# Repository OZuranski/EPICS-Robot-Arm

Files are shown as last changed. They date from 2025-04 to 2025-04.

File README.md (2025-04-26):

# Project Manus
 
Project Manus is a student lead team part of Purdue University's EPICS ECE Outreach program. Our main goal with Project Manus is to showcase engineering design principles to prospective students through an interactive, easy to build robotic arm. The arm was modeled in Fusion 360 with mostly 3D printed parts and common electronics to remain accessible for schools and hobbyists. It features 5 degrees of freedom, RC controls, and Nema 17 stepper motors, all controled by an Arduino for expandibility. The endeffector can be replaced with various attatchments such as a claw or a pen. [Demo](https://drive.google.com/file/d/1h7FeMoHUVKW86da__4PCTzvnMPEXpfWK/view?usp=sharing)

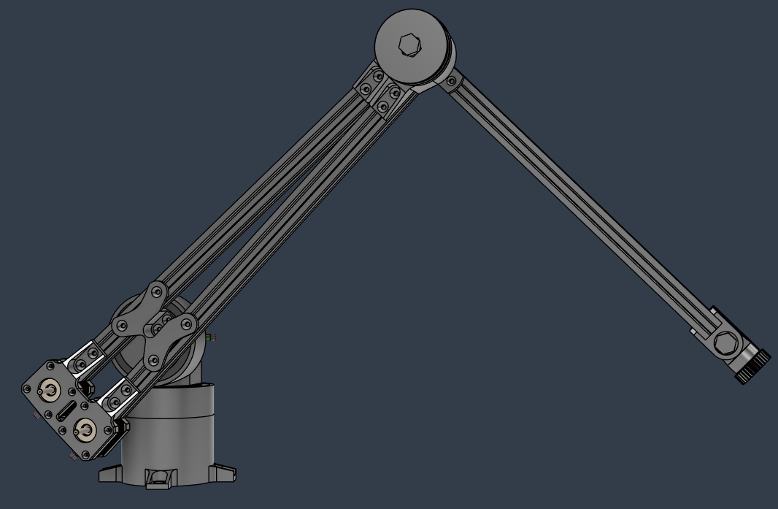
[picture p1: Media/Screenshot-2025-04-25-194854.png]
CAD

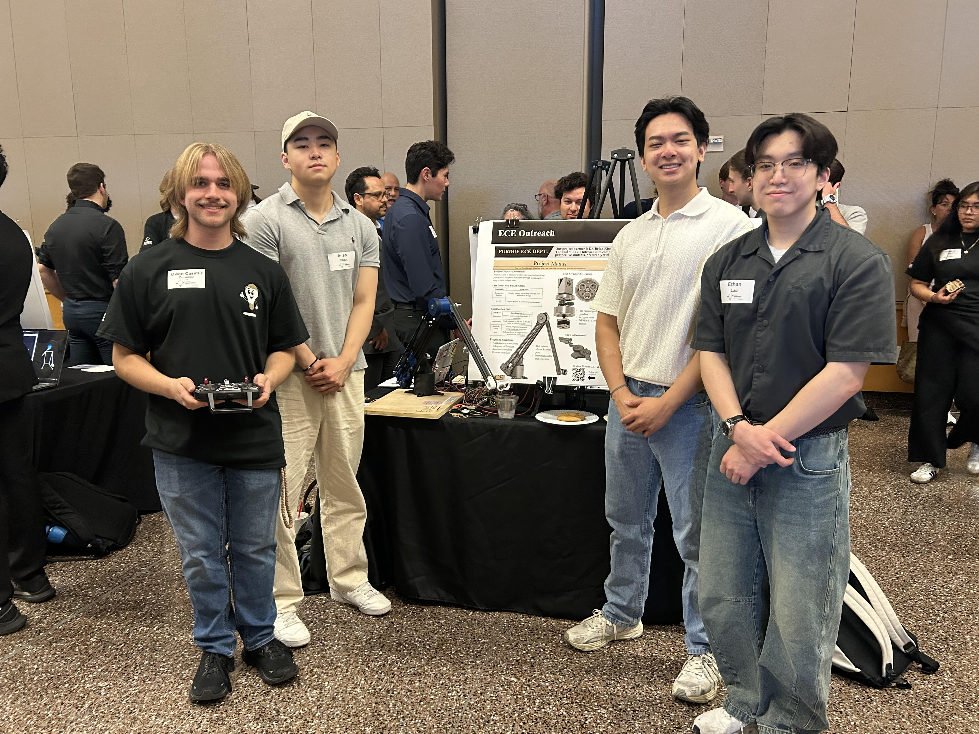
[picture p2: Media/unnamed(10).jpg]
Showcase

Poster
# Issues

1. Many components such as the bearings rely on a tight interference fit with 3D printed plastic. This method makes assembly relatively simple, however it makes disassembly almost impossible without cracking the plastic. If the parts are printed in PLA, the fit can slowly  loosen over time due to PLA's fluid properties under pressure, leading to excessive play in the arm. We suggest modifying the model to include screw sections between press fit components and other parts to make disassembly easier, and to print all parts in PETG.
2. The gear ratio of the base, shoulder, and elbow joint is not high enough for the weight of the arm. It is currently at 6:1, but we suggest modifying the gears within the planetary gearboxes and the pulleys to be at least 24:1. Geared Nema 17 or larger motors can be used, but this will require a major redesign of the arm which will be more costly.
3. Unfortunately due to time constraints within our semester, we were unable to fully implement the wrist joint, hand joint, and a functional end effector in our prototype. We suggest finding or desining a simple claw mechanism that uses light servo motors to minimize weight at the end of the arm.

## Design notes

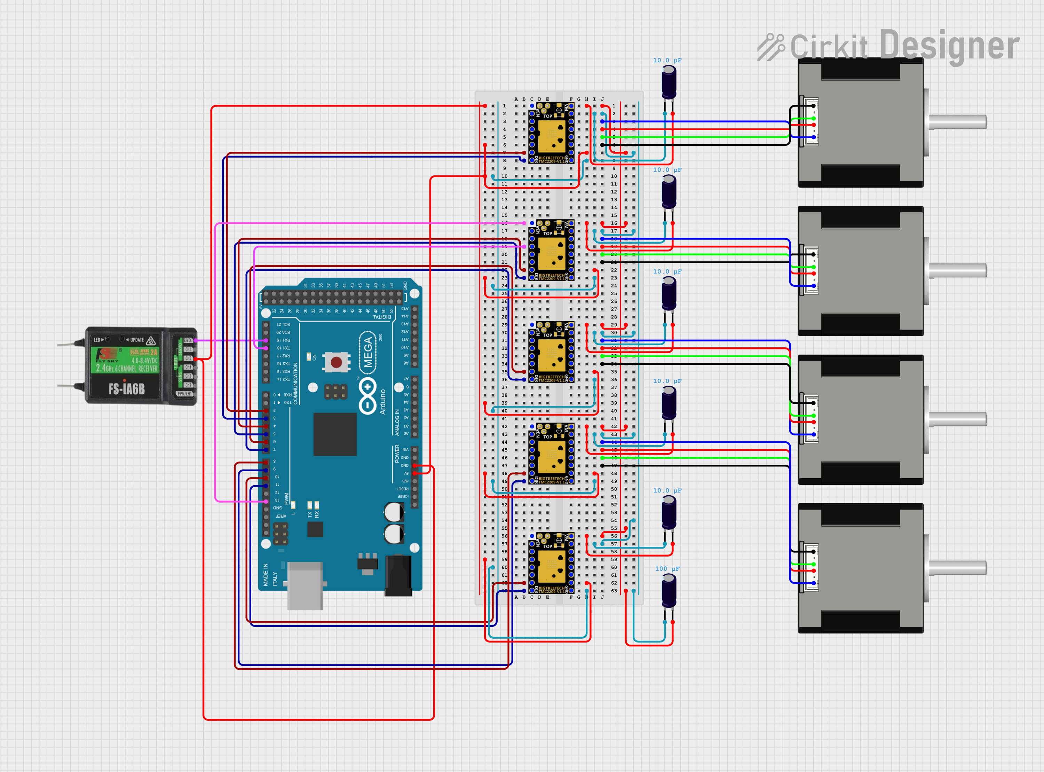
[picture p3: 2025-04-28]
Media/circuit_image.png

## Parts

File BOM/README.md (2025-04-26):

# Bill of Materials
 
The estimated build cost for the project is roughly $300. We reccomend printing all parts in PETG filament with standard settings. Please note that every 3D printer prints with a different tolerance. You will likely have to adjust dimesions within CAD to get proper interference fits, which this design relies on. A total of 6 planet gears and 2 sun gears are required.

1x $9.99 - GT2 Timing Belt  https://a.co/d/6Wf6PmA 

1x $7.69 - M10 Bolt https://a.co/d/aXNfsUf 

1x $5.99 - M10 Jam Nut https://a.co/d/iorE0f6 

1x $13.49 - 10x20 bearing https://a.co/d/e00AVKj 

1x $7.99 - 16t GT2 Pulley https://a.co/d/gQsRvjb 

1x $8.99 - 30x47 bearing https://a.co/d/8ohwXap 

1x $42.99 - Set of 5 Nema 17 motors https://a.co/d/6YtVc1i 

1x $13.79 - 60x78 bearings https://a.co/d/6YtVc1i 

1x $19.98 - Nema 11 motor https://a.co/d/0j2qDxP 

1x 20.99 Arduino MEGA 2650 https://a.co/d/017Ihgk 

1x $50.69 Wireless Controller https://a.co/d/4oq5mv8 

1x $19.98 set of 5 motor drivers https://a.co/d/9IKwbep 

1x $14.99 Machine screw set  https://a.co/d/8UwfHxt 

1x $18.59 2020 Aluminum extrusion  https://a.co/d/4guqIsl 

1x $5.99 M4 T nuts  https://a.co/d/hmVDdFK 

1x $4.99 M4 x 35mm screws https://a.co/d/f0rgOdL 

1x $4.99 m2.5 x 8mm screws https://a.co/d/42wxDNc

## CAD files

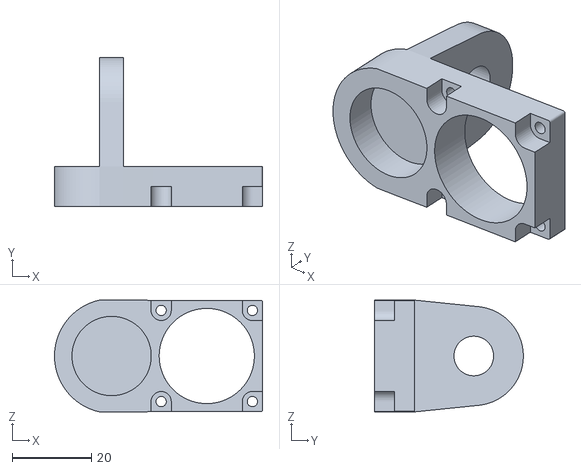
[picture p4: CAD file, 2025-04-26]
BOM/Printed Parts/Hand bracket.stl
52.5 x 37.5 x 28.2

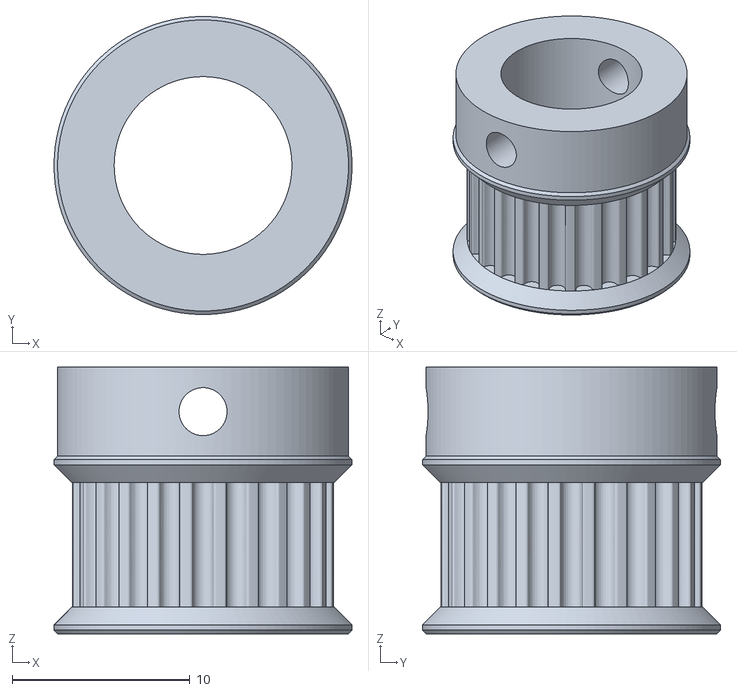
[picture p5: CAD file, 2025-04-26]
BOM/Printed Parts/Wrist Pulley 24t.stl
16.8 x 16.8 x 15.0

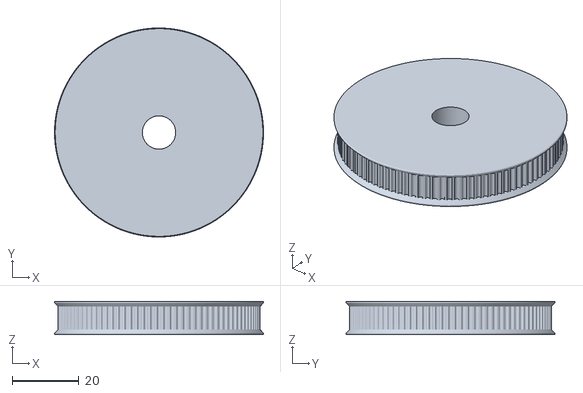
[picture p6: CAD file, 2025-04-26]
BOM/Printed Parts/Wrist Pulley 96t.stl
62.6 x 62.6 x 10.0

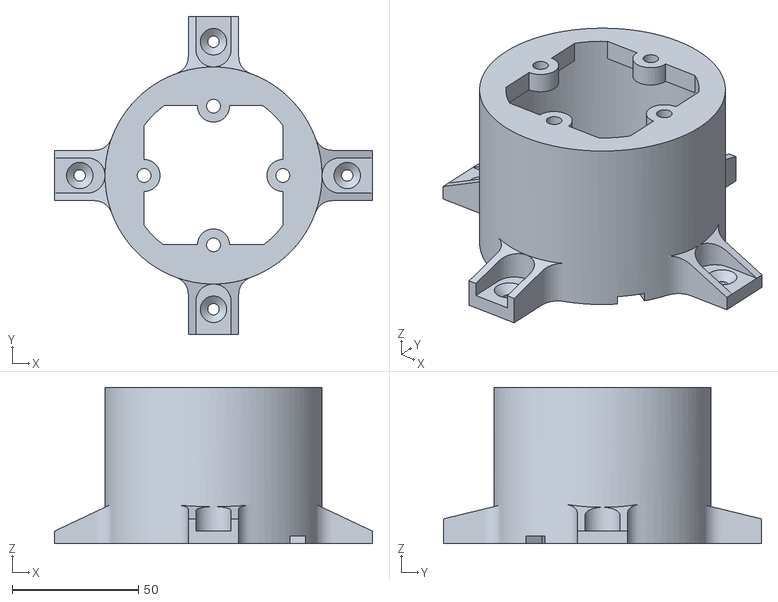
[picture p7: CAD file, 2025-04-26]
BOM/Printed Parts/Base Mount.stl
126.0 x 126.0 x 62.0

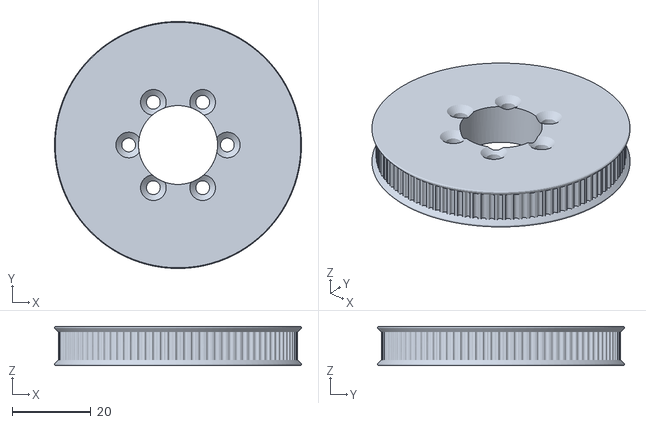
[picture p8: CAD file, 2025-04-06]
BOM/Printed Parts/Forearm Pulley 96t.stl
62.6 x 62.6 x 10.0

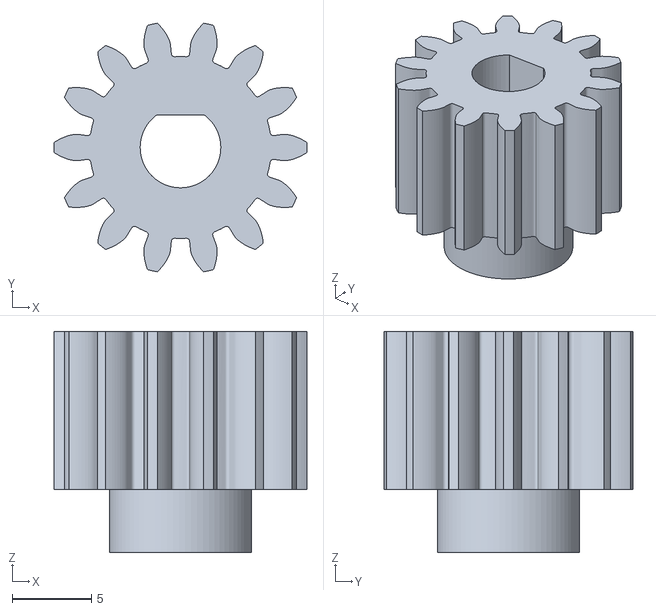
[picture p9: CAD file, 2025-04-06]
BOM/Printed Parts/Sun gear.stl
16.0 x 15.7 x 14.0

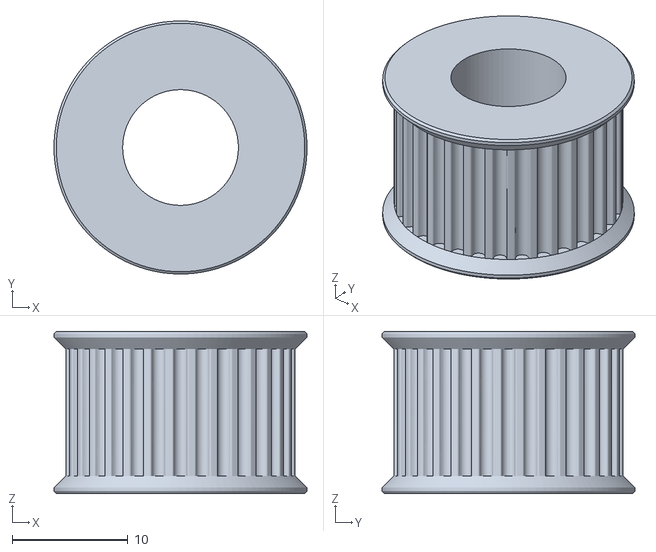
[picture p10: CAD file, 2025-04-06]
BOM/Printed Parts/Wrist Pulley 32t.stl
21.9 x 21.9 x 14.0

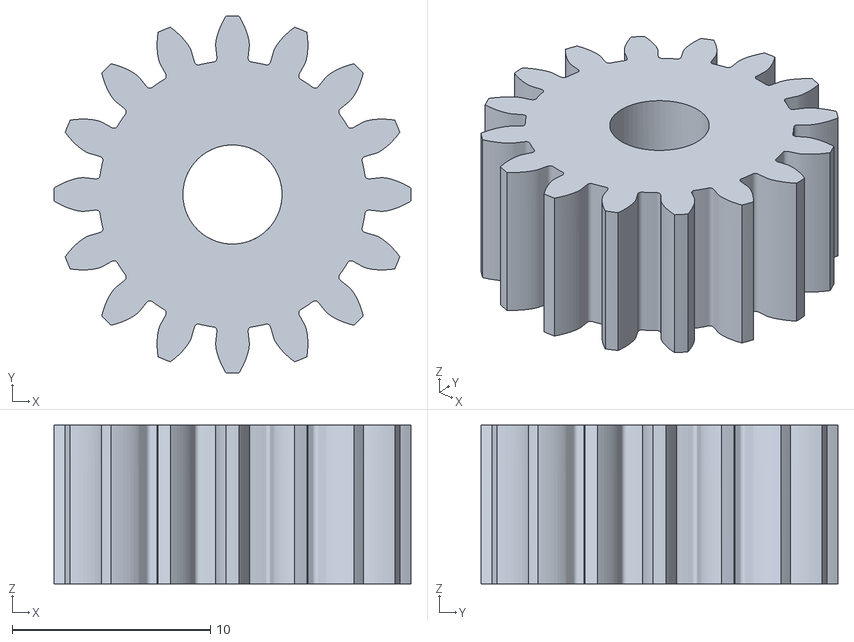
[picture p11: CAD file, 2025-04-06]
BOM/Printed Parts/Hand Gear 16t.stl
18.0 x 18.0 x 8.00

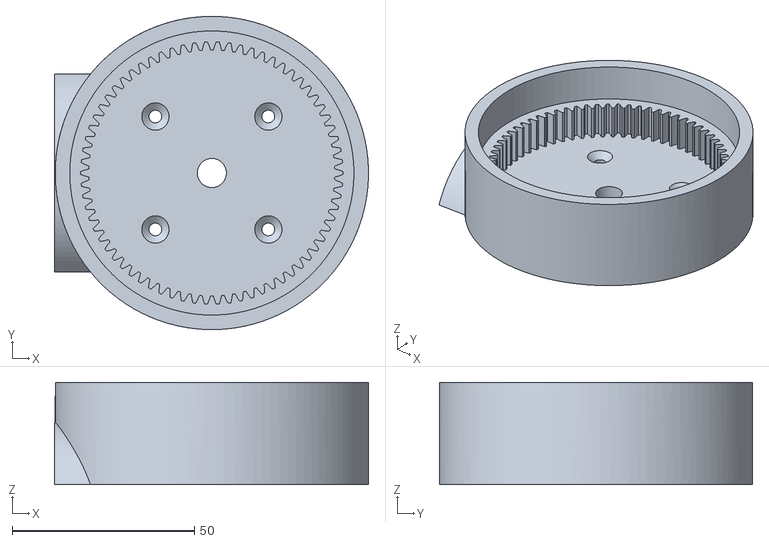
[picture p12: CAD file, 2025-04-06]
BOM/Printed Parts/Ring Gear Shoulder.stl
86.2 x 86.0 x 28.0

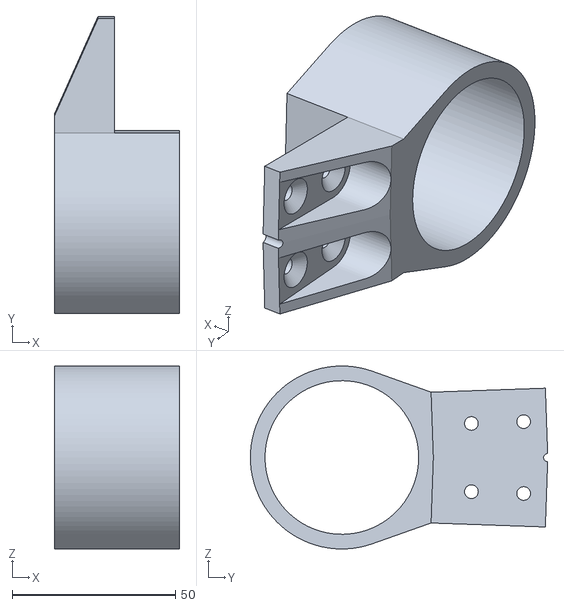
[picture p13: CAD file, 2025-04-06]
BOM/Printed Parts/Elbow Housing.stl
38.4 x 91.0 x 56.0

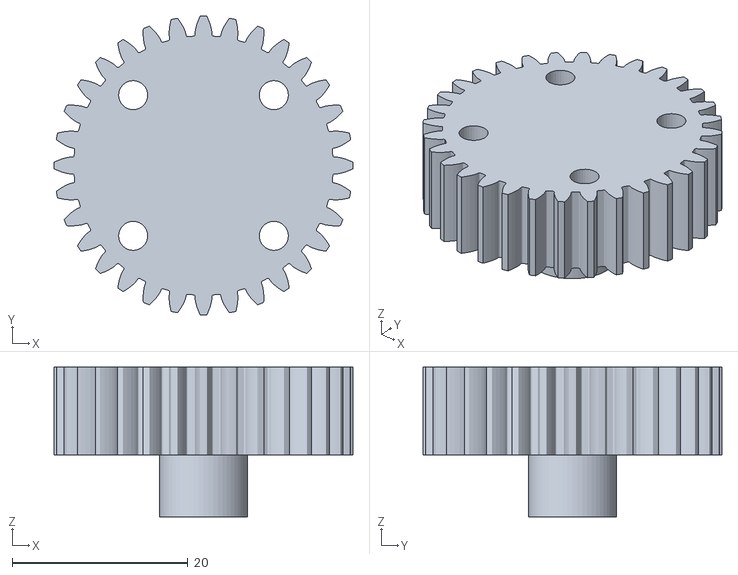
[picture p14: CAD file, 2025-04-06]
BOM/Printed Parts/Hand Gear 32t.stl
34.0 x 34.0 x 17.0

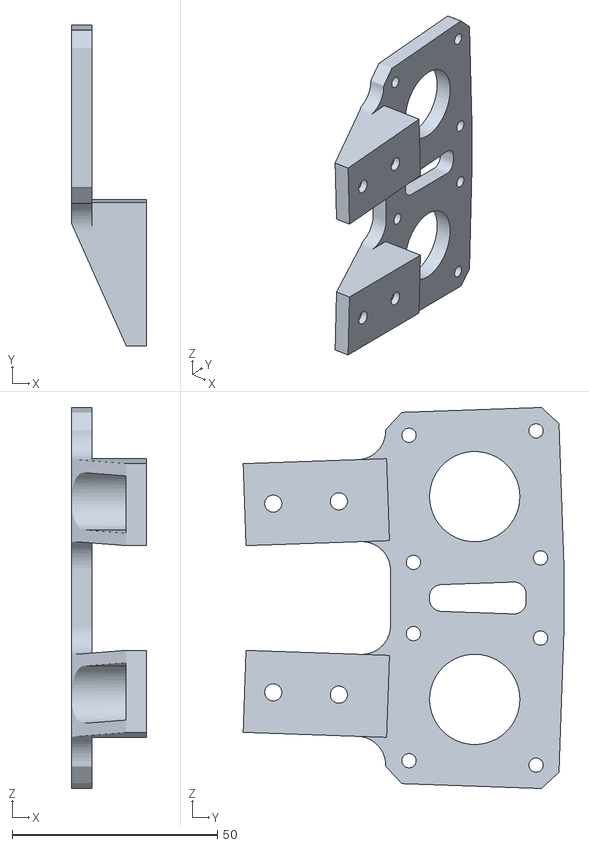
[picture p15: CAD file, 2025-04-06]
BOM/Printed Parts/Dual Motor Mount.stl
18.4 x 78.2 x 92.9

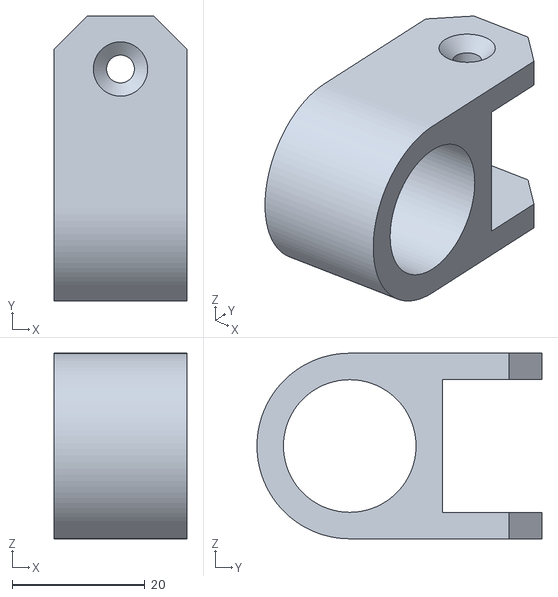
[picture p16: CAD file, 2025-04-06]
BOM/Printed Parts/Wrist Housing.stl
20.0 x 43.0 x 28.0

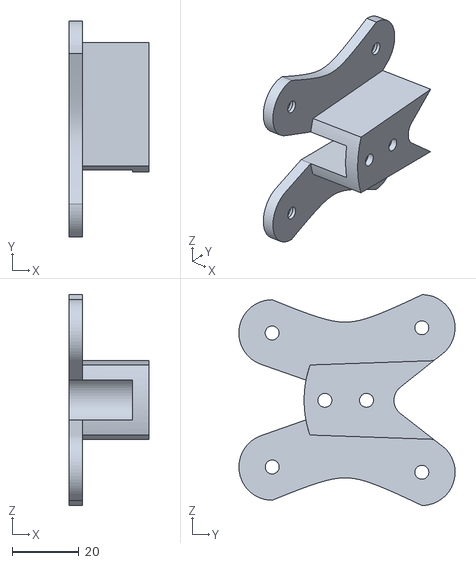
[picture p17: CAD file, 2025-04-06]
BOM/Printed Parts/Shoulder Bracket.stl
24.0 x 65.0 x 63.4

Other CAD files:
BOM/Printed Parts/Base Cage.stl
BOM/Printed Parts/Ring Gear Base.stl
BOM/Printed Parts/Forearm Attatchment.stl
BOM/Printed Parts/Shoulder Cage.stl
BOM/Printed Parts/Planet gear 28t.stl
BOM/Printed Parts/Shoulder Motor Bracket.stl
CAD/Manus Claw v1.f3d

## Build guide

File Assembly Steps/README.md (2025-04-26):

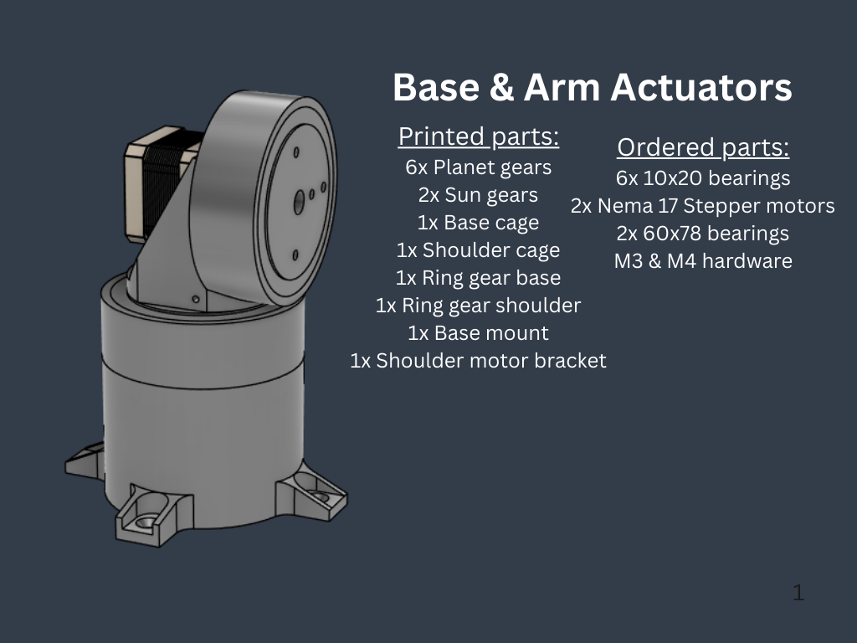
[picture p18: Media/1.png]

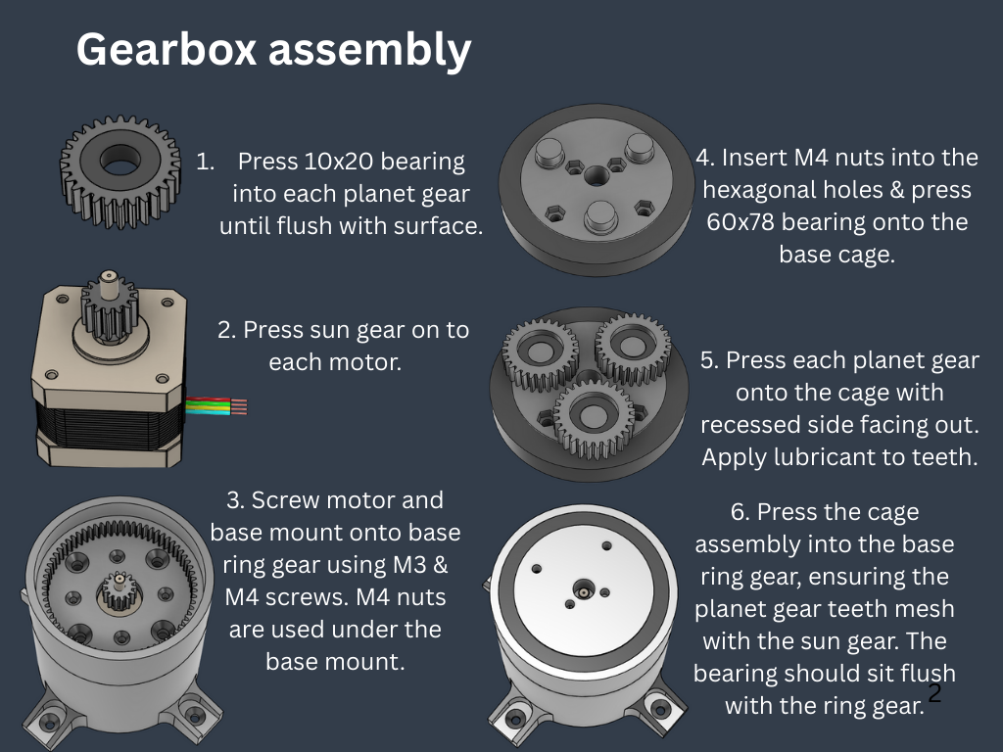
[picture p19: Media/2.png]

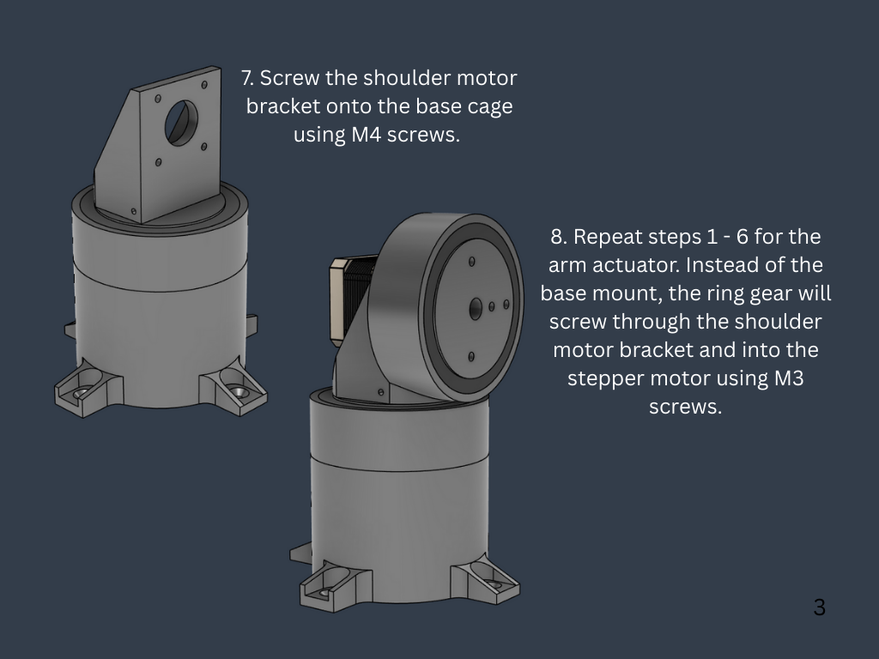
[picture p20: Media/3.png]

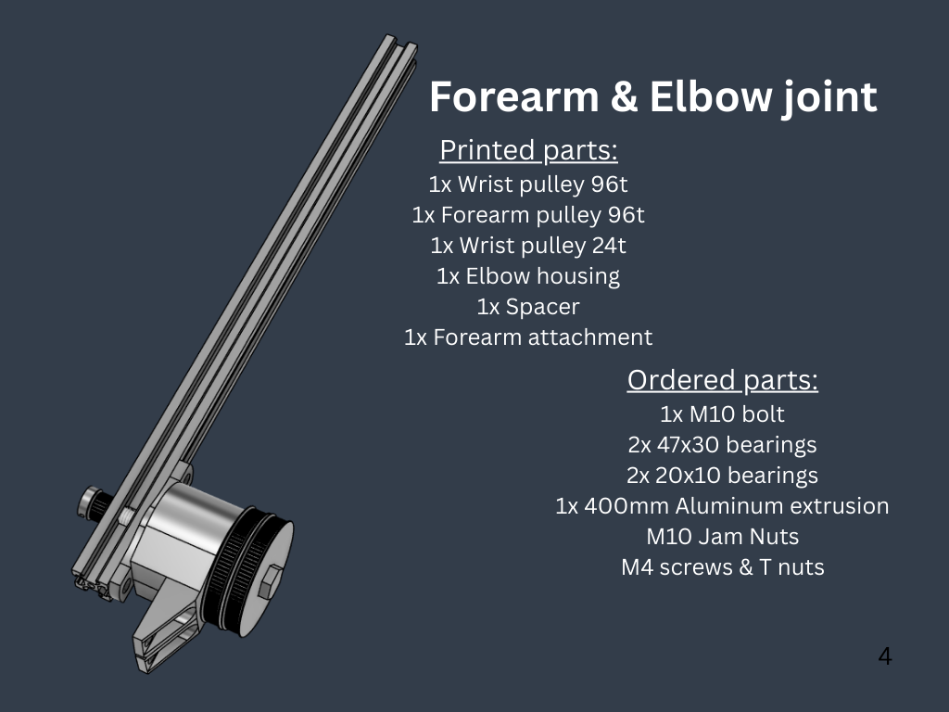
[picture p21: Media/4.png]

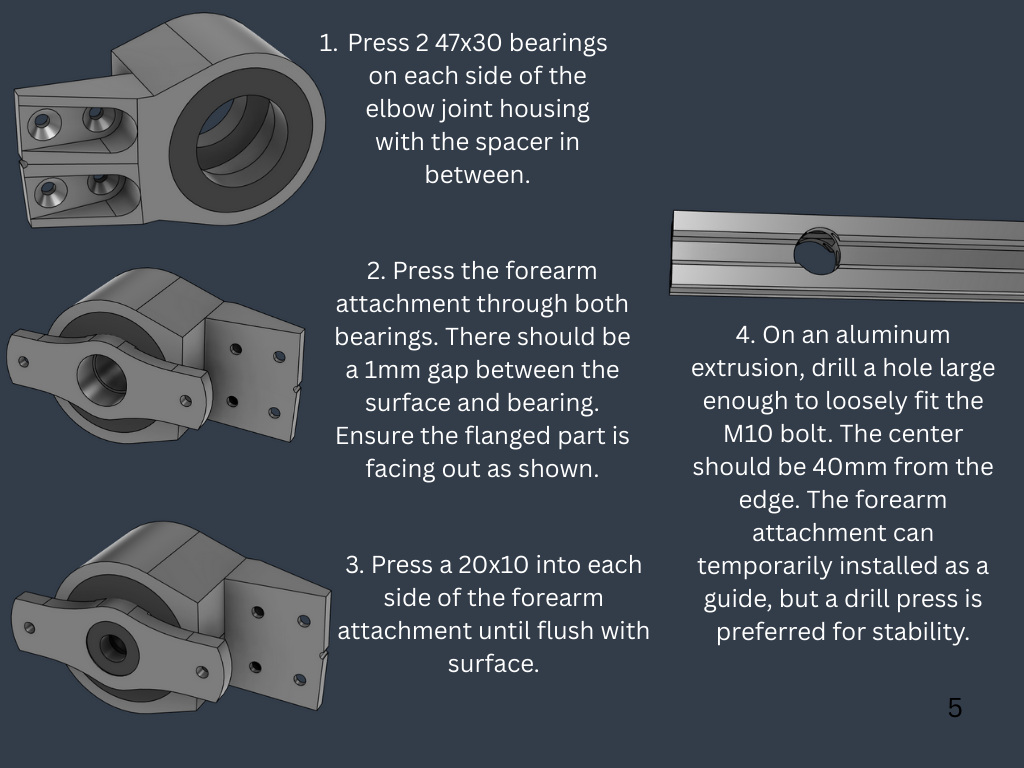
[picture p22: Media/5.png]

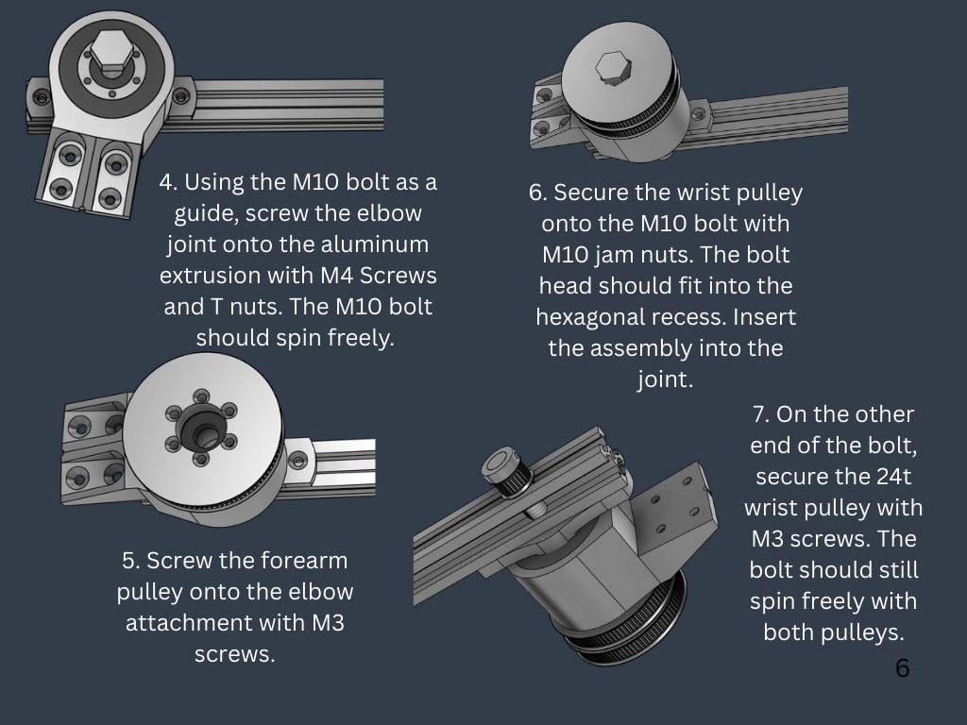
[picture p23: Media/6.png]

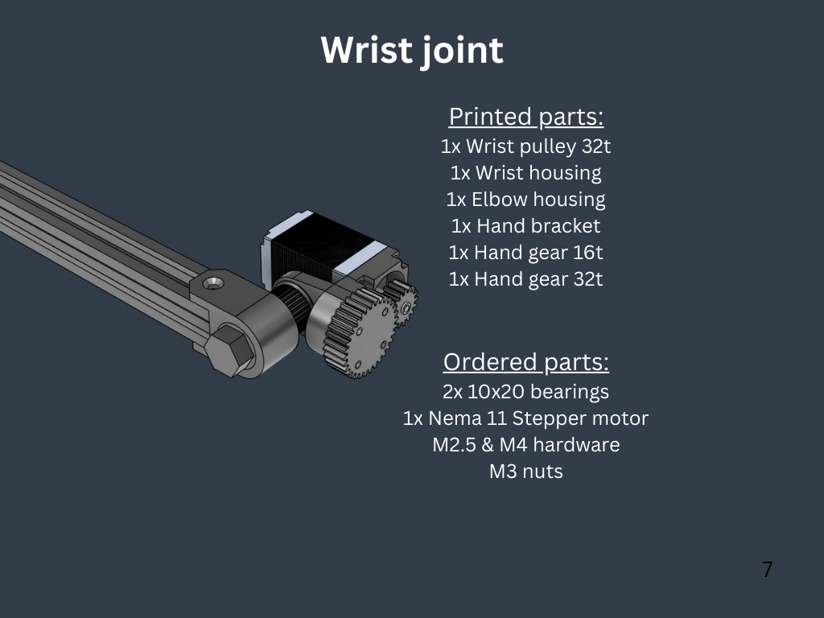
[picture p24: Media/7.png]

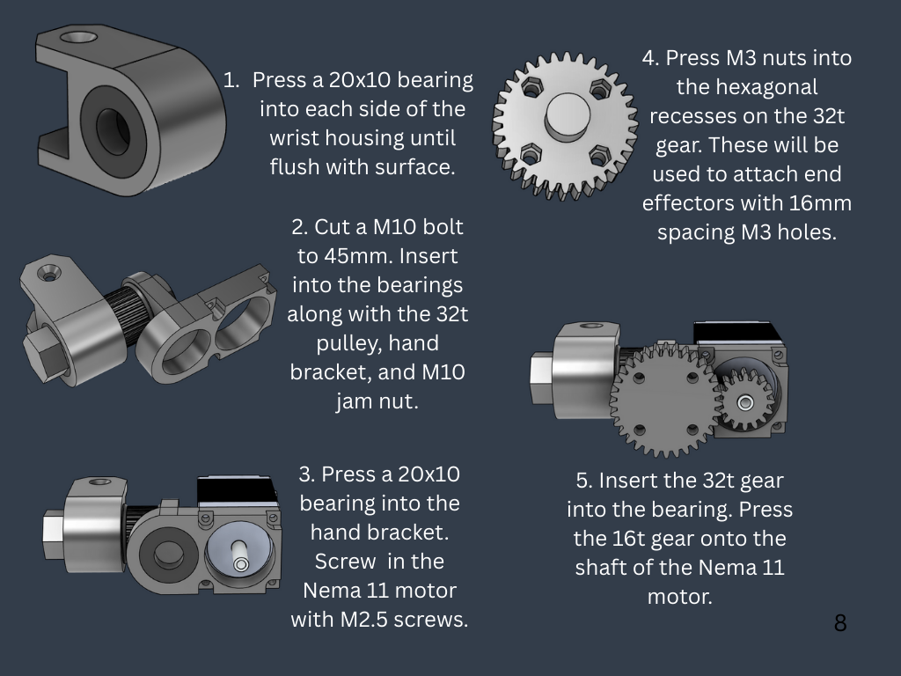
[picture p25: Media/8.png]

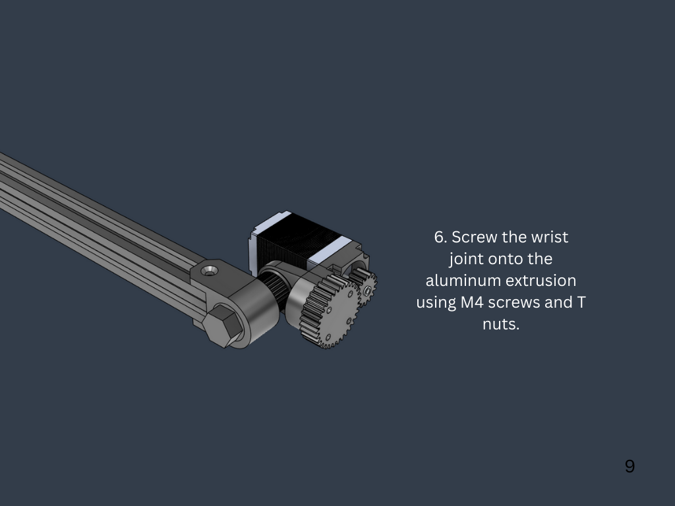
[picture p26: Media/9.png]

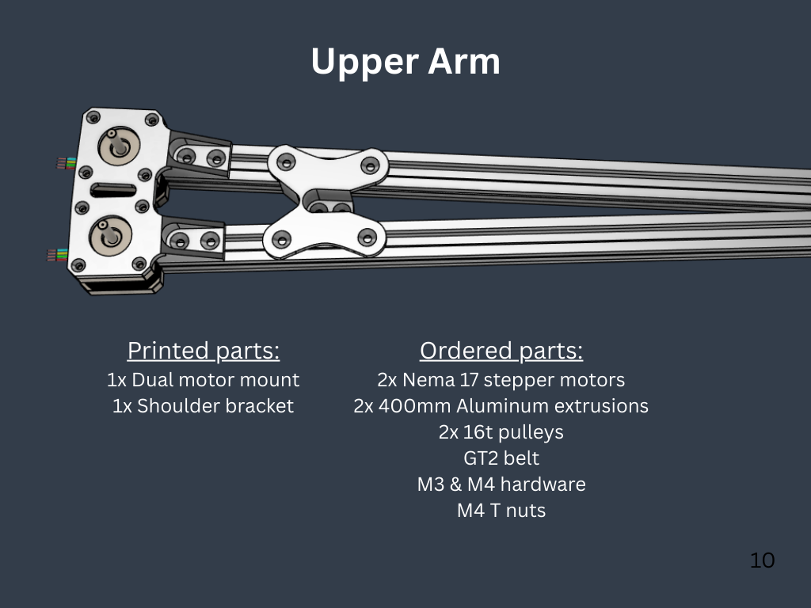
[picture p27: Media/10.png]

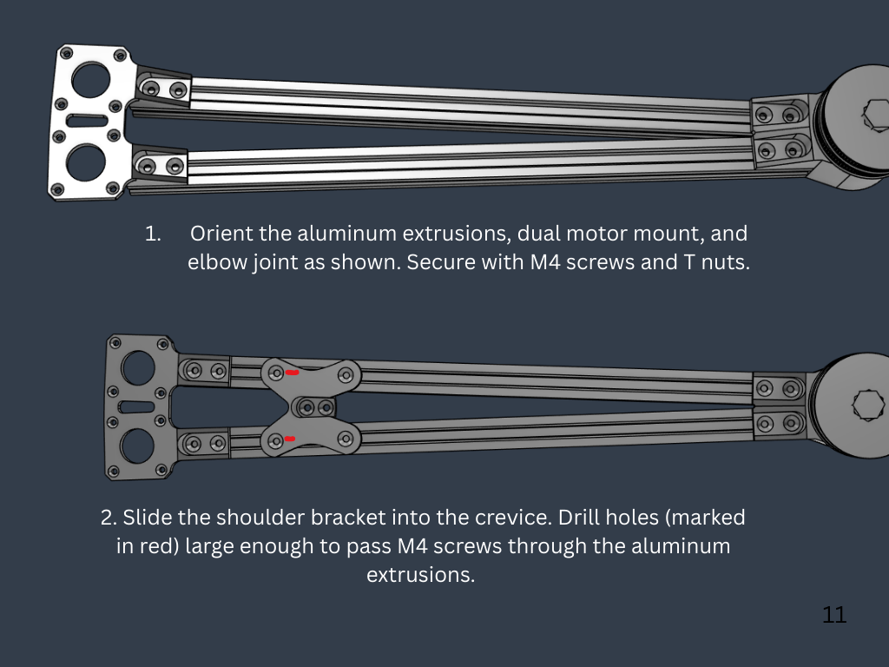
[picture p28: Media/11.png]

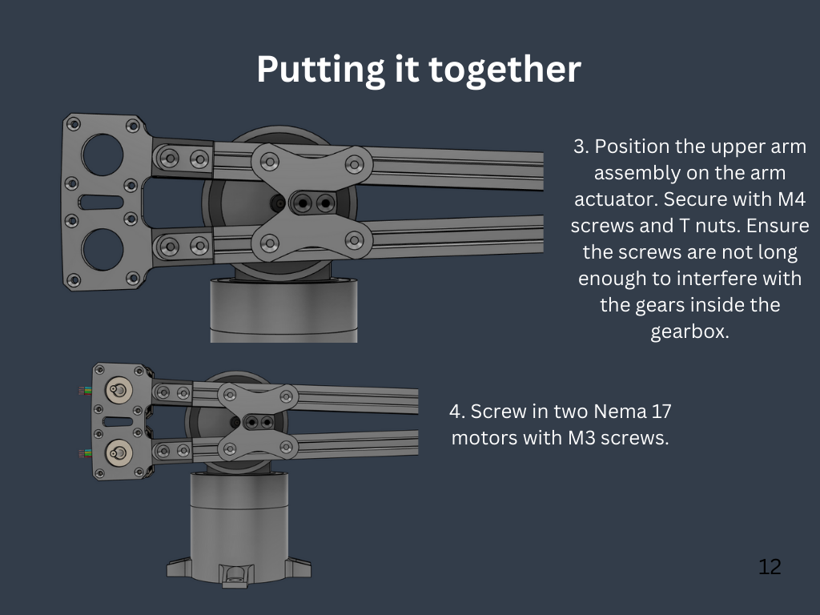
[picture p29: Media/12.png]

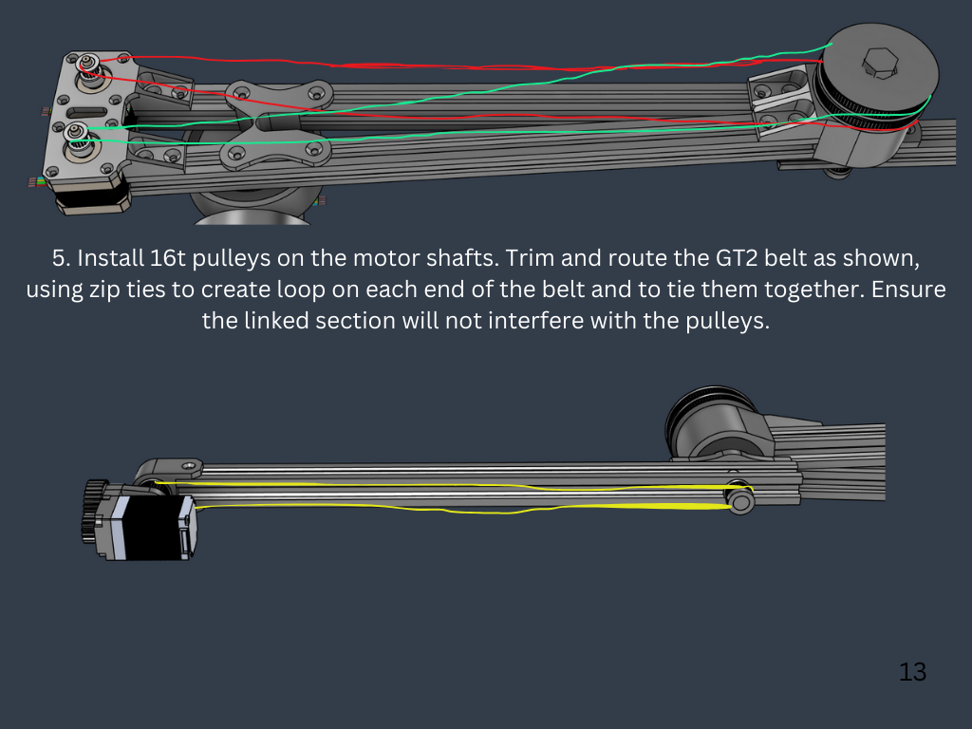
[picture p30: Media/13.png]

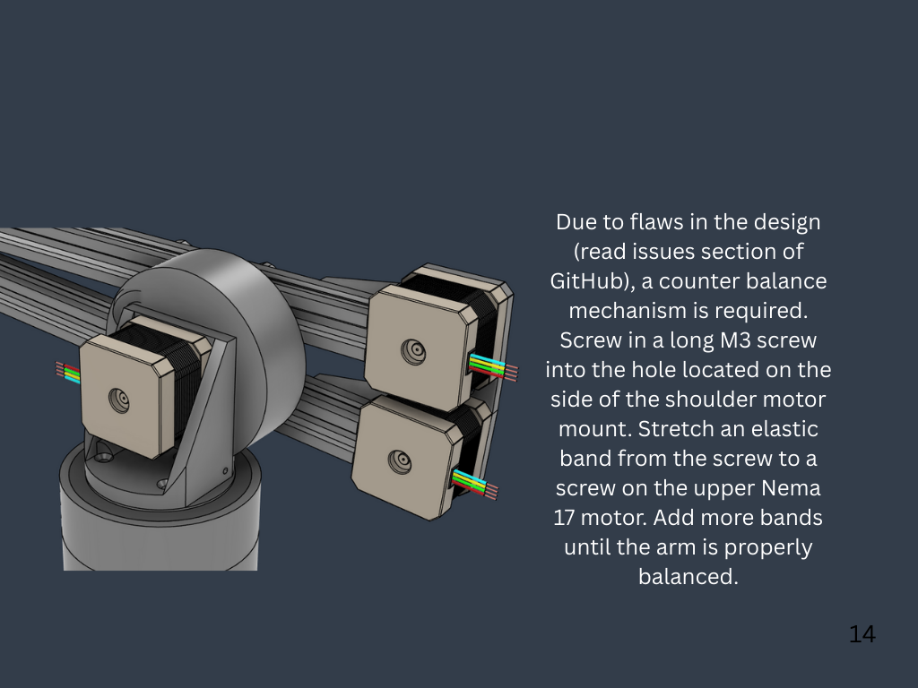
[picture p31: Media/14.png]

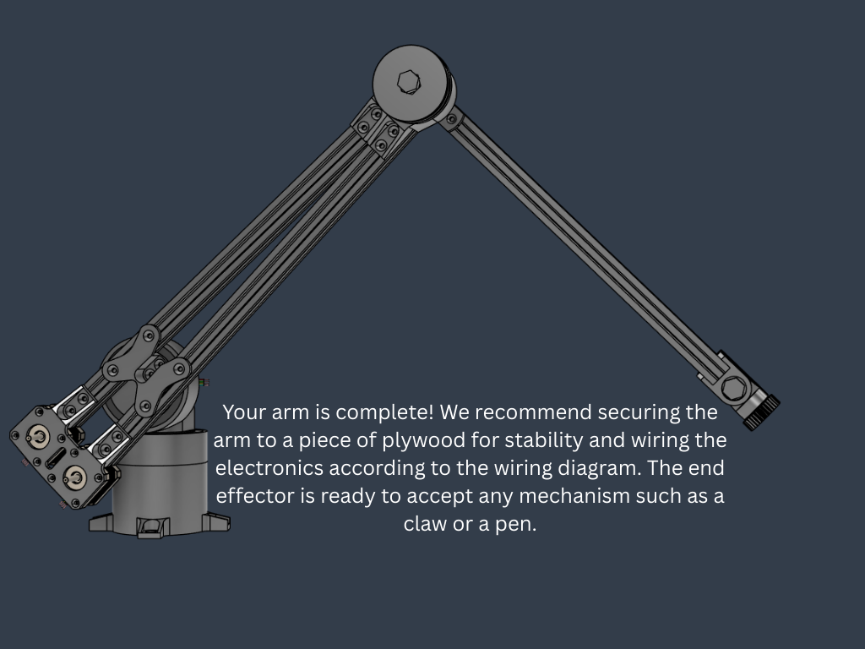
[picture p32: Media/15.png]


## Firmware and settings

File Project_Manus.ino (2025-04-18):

#include <AccelStepper.h>
#include <IBusBM.h>
#include <Servo.h>
#include <TMCStepper.h>

// Stepper2 TMC2209 Config
#define STEP_PIN_2 4
#define DIR_PIN_2 5
#define EN_PIN_2 13
#define R_SENSE 0.11f
#define DRIVER_ADDRESS 0b00

// Serial1 used for UART to TMC2209
TMC2209Stepper driver2(&Serial1, R_SENSE, DRIVER_ADDRESS);

// AccelStepper setup
AccelStepper stepper1(1, 2, 3);
AccelStepper stepper2(AccelStepper::DRIVER, STEP_PIN_2, DIR_PIN_2); // updated for TMC2209
AccelStepper stepper3(1, 6, 7);
AccelStepper stepper4(1, 8, 9);
AccelStepper stepper5(1, 10, 11);

Servo myservo;
IBusBM ibus;

void setup() {
  delay(500);

  // Enable pin for stepper2
  pinMode(EN_PIN_2, OUTPUT);
  digitalWrite(EN_PIN_2, LOW); // Enable driver

  // Start UART for TMC2209
  Serial1.begin(115200);
  driver2.begin();
  delay(500);
  driver2.rms_current(1850);        // Set motor current in mA
  delay(500);
  driver2.microsteps(16);          // Optional
  driver2.en_spreadCycle(true);   // Enable StealthChop
  //driver2.TPOWERDOWN(255); // Disables automatic power down when idle
  driver2.pdn_disable(true);       // Use UART
  driver2.I_scale_analog(false);   // Use digital current scaling
  driver2.TPOWERDOWN(255); // Disables automatic power down when idle

  // Set max speeds
  stepper1.setMaxSpeed(650);
  stepper2.setMaxSpeed(650); // Right Y (TMC2209)
  stepper3.setMaxSpeed(650);
  stepper4.setMaxSpeed(900);
  stepper5.setMaxSpeed(650);

  myservo.attach(12);
  Serial.begin(115200);
  ibus.begin(Serial1);

  delay(500);
}

void loop() {
  controlStep(stepper1, 0); // Right X
  controlStep(stepper2, 1); // Right Y (TMC2209)
  controlStep(stepper3, 2); // Left Y
  controlStep(stepper4, 3); // Left X
  controlStep(stepper5, 4); // Dial
  controlServo(5);          // Claw
}

void controlStep(AccelStepper &stepper, int channel) {
  int chVal = ibus.readChannel(channel) - 1502;

  if (chVal > -50 && chVal < 50) {
    stepper.setSpeed(0);
  } else {
    int jVal = -chVal;
    stepper.setSpeed(jVal);
    Serial.print("Channel "); Serial.print(channel);
    Serial.print(": "); Serial.println(jVal);
  }

  stepper.runSpeed();
}

void controlServo(int channel) {
  static int prevAngle = -1;
  int chVal = ibus.readChannel(channel) - 1502;
  int jVal = -(chVal * 1.5);
  int angle = map(jVal, -755, 755, 0, 180);

  if (angle != prevAngle) {
    Serial.print("Channel "); Serial.print(channel);
    Serial.print(": "); Serial.print(jVal);
    Serial.print(" Degrees: "); Serial.print(angle); Serial.println("°");
    myservo.write(angle);
    prevAngle = angle;
  }
}

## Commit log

2025-04-04 Updated comments and readability
    Updated the comments to help the program be easier to read. Also tampered with the speeds to be more realistic and safe for use. Also updated function name for controlling steppers for when we make s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
2025-04-04 Video of Partially built RC prototype with TMC2209 Drivers
    Video of Partially built RC prototype with TMC2209 Drivers
2025-04-04 Rename 20250401_170437.mp4 to Partially built RC prototype with TMC2209.mp4
    Renamed to have accurate label
2025-04-04 Added picture documentation of current set up
    -Note: need to go back and collect earlier pictures throughout project too
2025-04-04 Rename 20250404_141810.jpg to Wiring setup TMC 2209 (no servo).jpg
    A diagram of the wiring is currently a WIP and will be added when done
2025-04-04 Rename 20250404_141818.jpg to Current arm assembly.jpg
2025-04-06 Create CAD
2025-04-06 Create Printed Parts
2025-04-09 +servo claw, stepper5, comments
    added function for claw control with servo, added back stepper 5, and added more comments for both old and new code to try and make it more readable
2025-04-18 Added UART functionality
    Added UART which allows set current, microsteps, stealthchop, current scaling, power down option. We needed this mainly for setting currently so we could control torque in that center most motor carr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
2025-05-14 Rename VID_20250424_091301_682.mp4 to Servo Claw Demo.mp4
2025-05-14 Rename VID_20250424_092855_0832.mp4 to Final Demo Spring.mp4
